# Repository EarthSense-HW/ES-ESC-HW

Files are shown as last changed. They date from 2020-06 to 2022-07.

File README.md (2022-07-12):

# ES-ESC-HW
Hardware source files for EarthSense ESC Based on VESC4

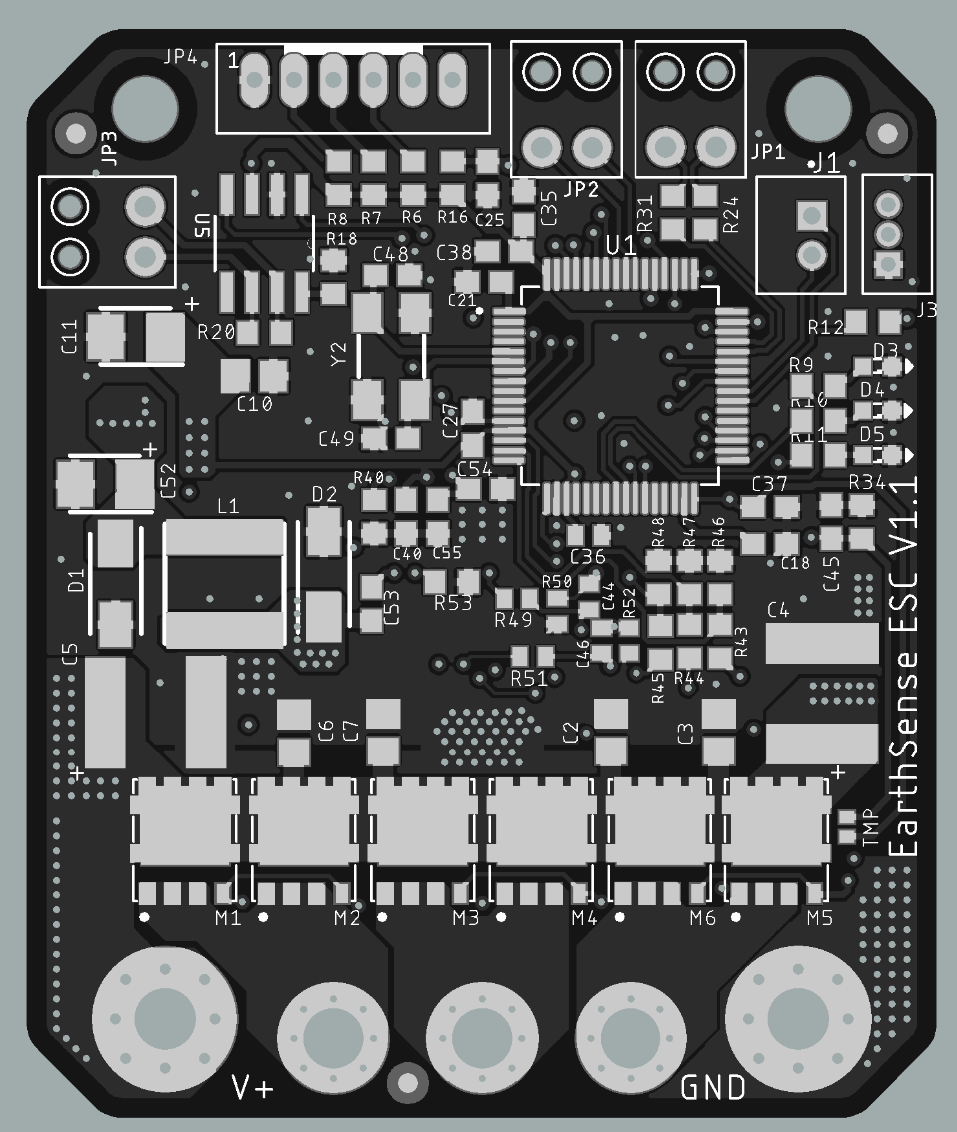
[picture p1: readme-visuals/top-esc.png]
top view

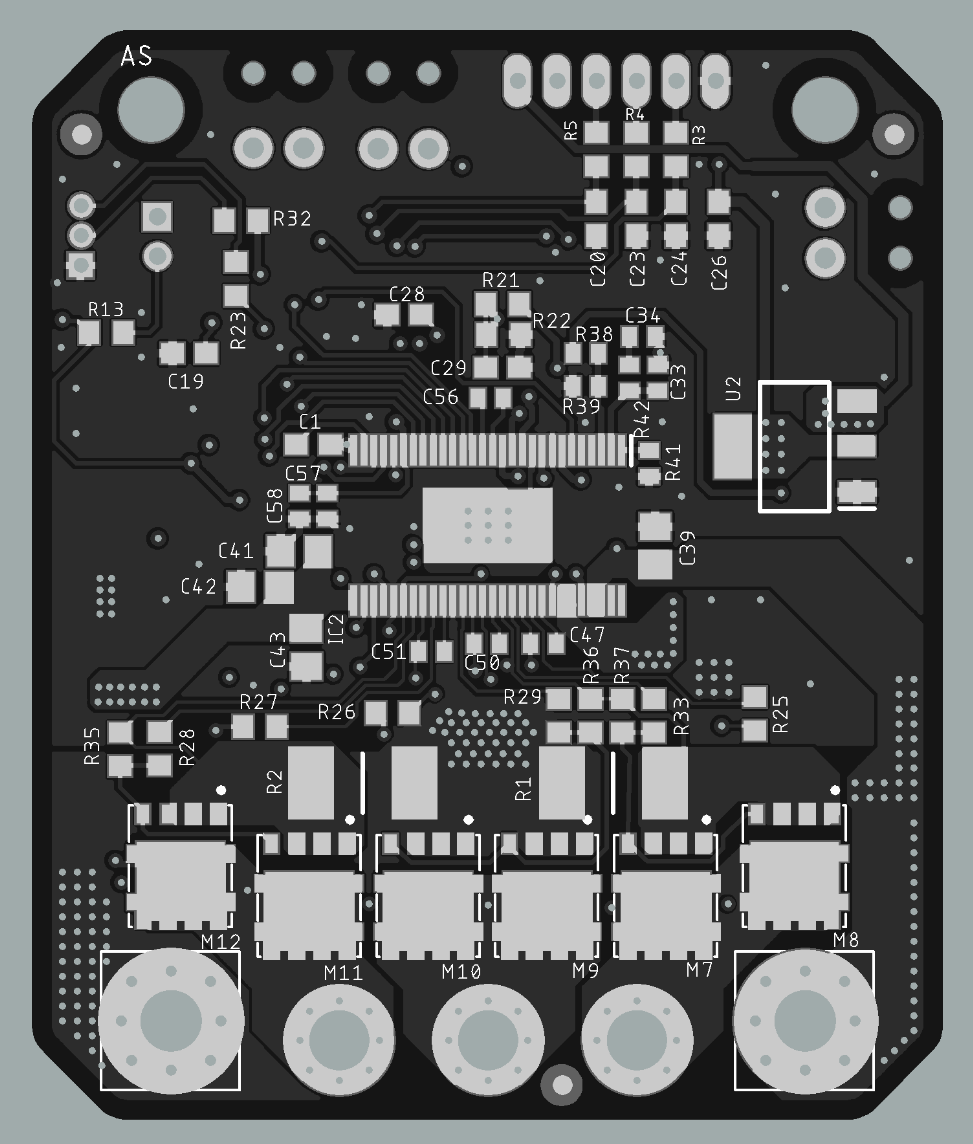
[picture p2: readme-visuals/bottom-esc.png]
bottom view


## Modifications from VESC4 Hardware:
* Changed form factor to fit onto EarthSense TerraSentia System Board
* Two IO Pins are broken out for auto-setting CAN ID based on placement on EarthSense TerraSentia System Board
* MOSFETs changed to flat 5x6 packages (STL260N)
* Changed various components in 5v regulator and 3.3v regulator circuits
* Removed IO pins that are not useful to EarthSense TerraSentia Robots
* SWD Programming header broken out to JST-ZH connector
* Two DIO broken out to JST-PH Connector for reading quadrature encoders

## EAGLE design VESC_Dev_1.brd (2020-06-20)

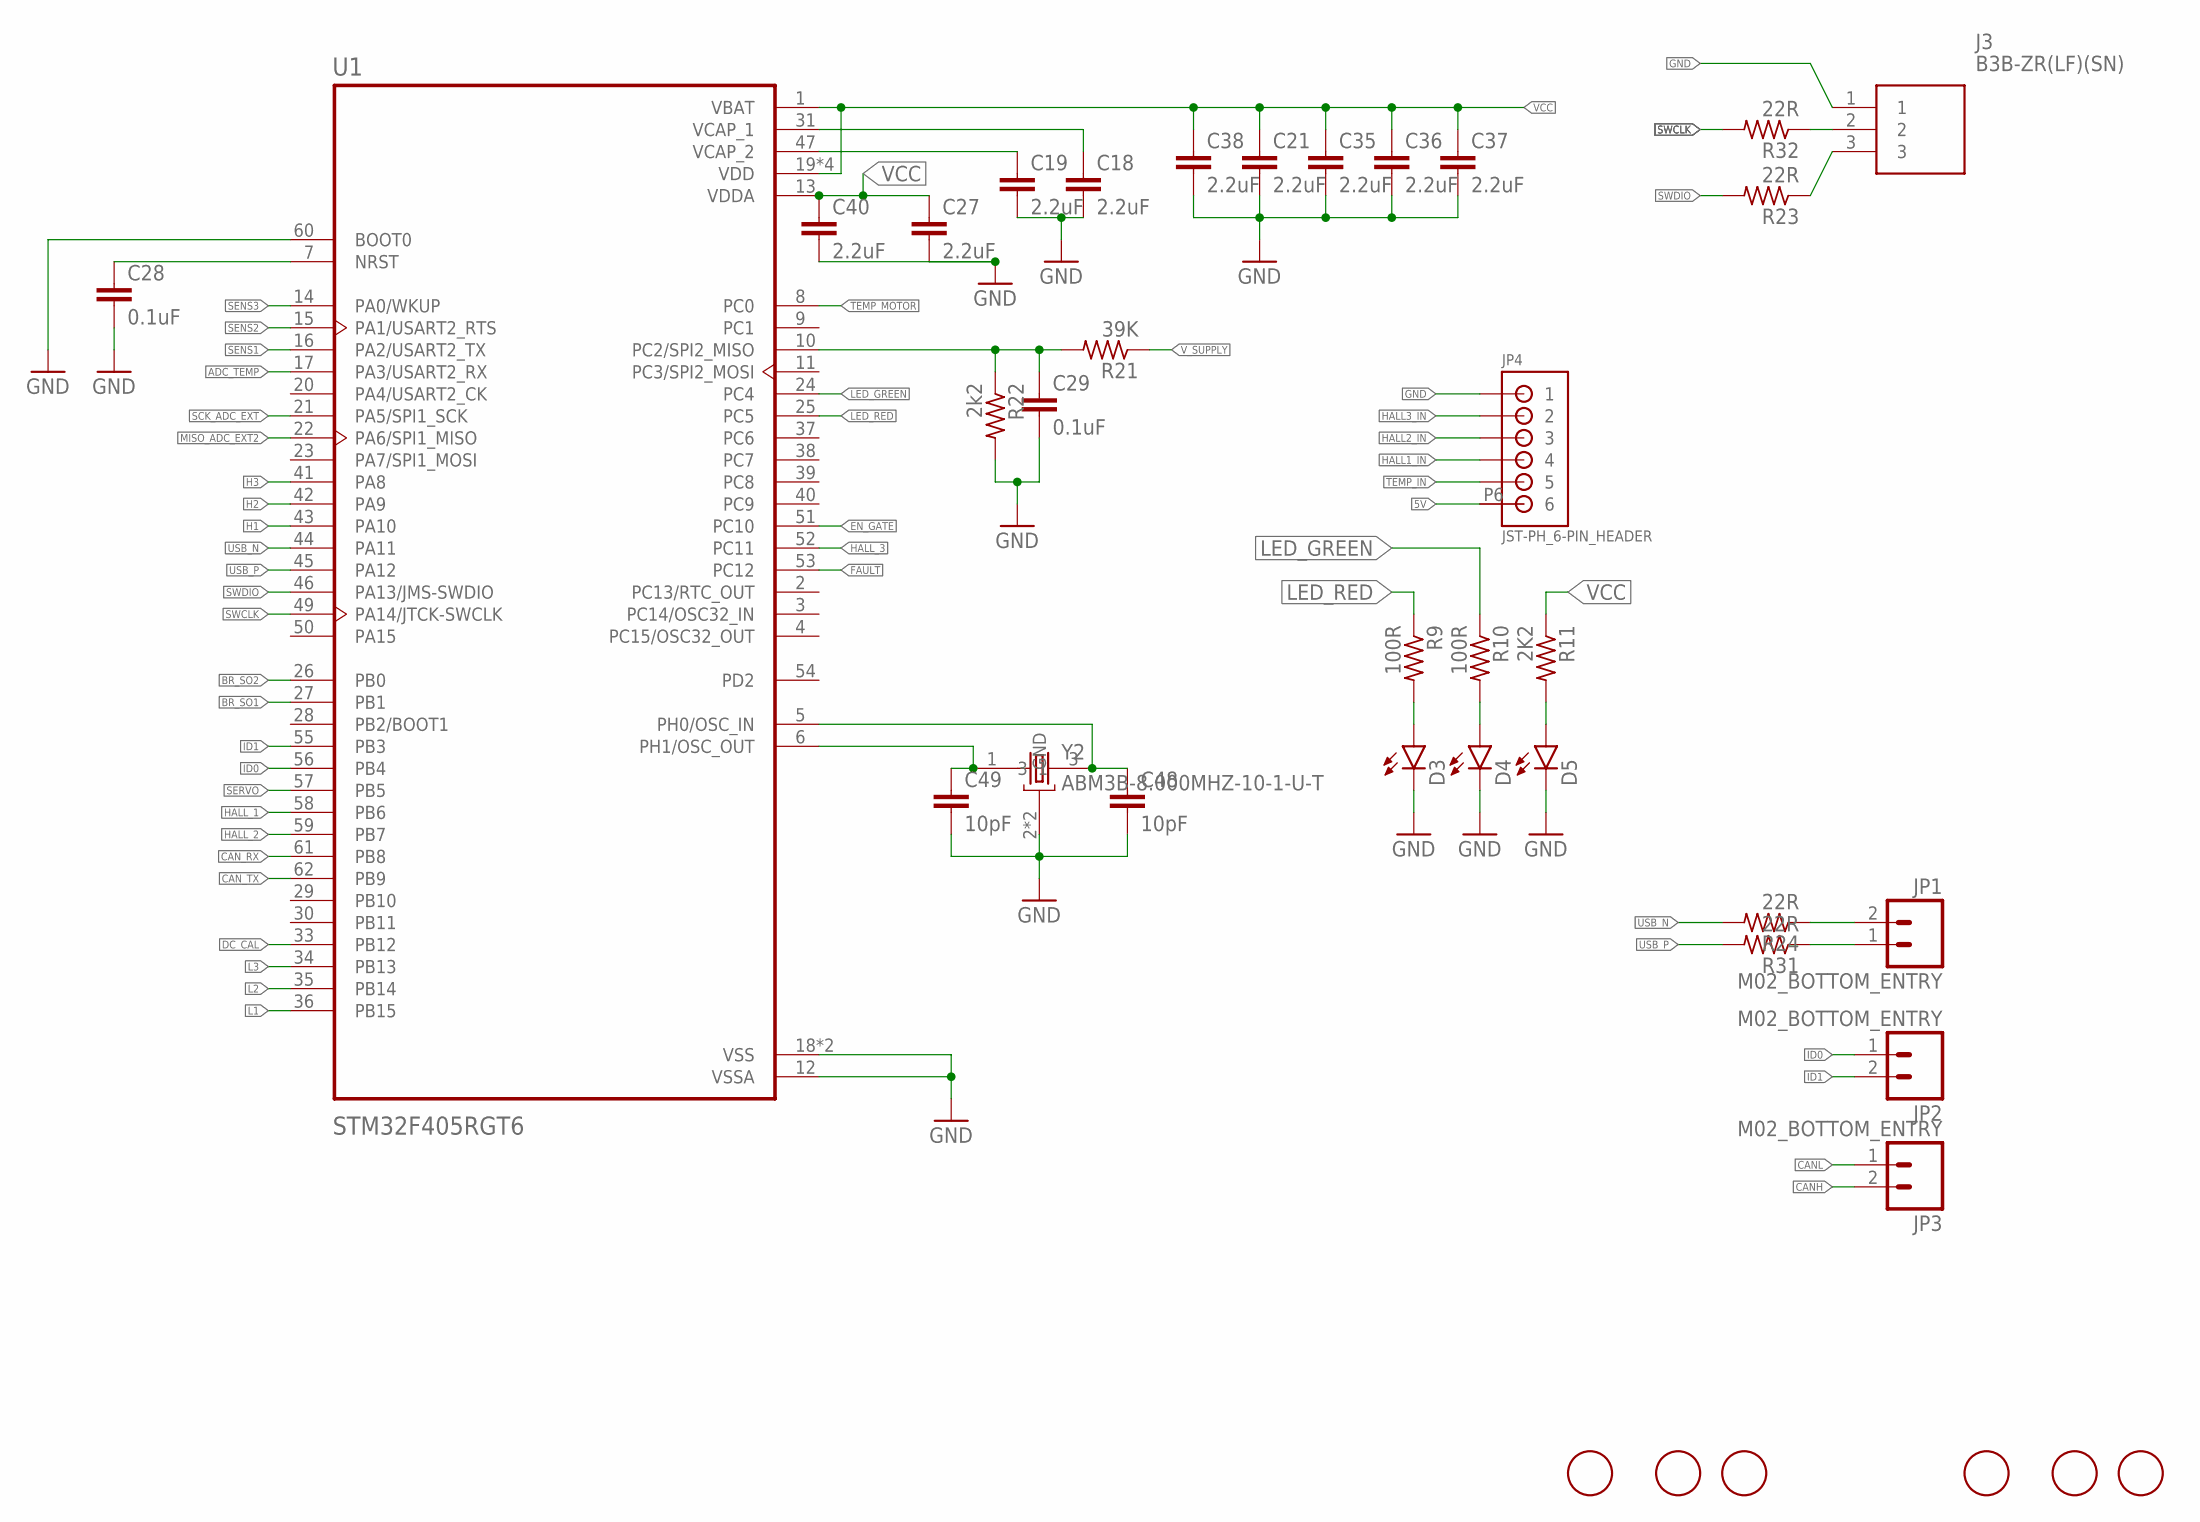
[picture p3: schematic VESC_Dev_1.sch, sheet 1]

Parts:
C18, C19, C21, C27, C35, C37, C38, C40: 2.2uF; C0603
C28, C29: 0.1uF; C0603
C36: 2.2uF; C0402
C48, C49: 10pF; C0603
D3, D4, D5: LEDSML0603; SML0603
J3: B3B-ZR(LF)(SN); SHDR3W50P0X150_1X3_600X350X450
JP1, JP2, JP3: M02_BOTTOM_ENTRY; 1X02_BOTTOM_ENTRY
JP4: JST-PH_6-PIN_HEADER; JST_B6B-PH_HEADER
R9, R10: 100R; R0603
R11: 2K2; R0603
R21: 39K; R0603
R22: 2k2; R0603
R23, R24, R31, R32: 22R; R0603
U1: STM32F405RGT6; QFP50P1200X1200X160-64N
U$1, U$2, U$3, U$4, U$5, U$6: FIDUCIAL; FIDUCIAL_1MM
Y2: ABM3B-8.000MHZ-10-1-U-T; OSCCC500X320X110-4N

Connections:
5V: JP4.P6 (6); also elsewhere on the board
ADC_TEMP: U1.17 (PA3/USART2_RX); also elsewhere on the board
BR_SO1: U1.27 (PB1); also elsewhere on the board
BR_SO2: U1.26 (PB0); also elsewhere on the board
CANH: JP3.2; also elsewhere on the board
CANL: JP3.1; also elsewhere on the board
CAN_RX: U1.61 (PB8); also elsewhere on the board
CAN_TX: U1.62 (PB9); also elsewhere on the board
DC_CAL: U1.33 (PB12); also elsewhere on the board
EN_GATE: U1.51 (PC10); also elsewhere on the board
FAULT: U1.53 (PC12); also elsewhere on the board
GND: C18.2, C19.2, C21.2, C27.2, C28.2, C29.2, C35.2, C36.2, C37.2, C38.2, C40.2, C48.2, C49.2, D3.C, D4.C, D5.C, J3.1, JP4.P1 (1), R22.2, U1.12 (VSSA), U1.18 (VSS), U1.60 (BOOT0), U1.63 (VSS), Y2.2 (GND), Y2.4 (GND); also elsewhere on the board
H1: U1.43 (PA10); also elsewhere on the board
H2: U1.42 (PA9); also elsewhere on the board
H3: U1.41 (PA8); also elsewhere on the board
HALL1_IN: JP4.P4 (4); also elsewhere on the board
HALL2_IN: JP4.P3 (3); also elsewhere on the board
HALL3_IN: JP4.P2 (2); also elsewhere on the board
HALL_1: U1.58 (PB6); also elsewhere on the board
HALL_2: U1.59 (PB7); also elsewhere on the board
HALL_3: U1.52 (PC11); also elsewhere on the board
ID0: JP2.1, U1.56 (PB4)
ID1: JP2.2, U1.55 (PB3)
L1: U1.36 (PB15); also elsewhere on the board
L2: U1.35 (PB14); also elsewhere on the board
L3: U1.34 (PB13); also elsewhere on the board
LED_GREEN: R10.1, U1.24 (PC4)
LED_RED: R9.1, U1.25 (PC5)
MISO_ADC_EXT2: U1.22 (PA6/SPI1_MISO)
unnamed: C28.1, U1.7 (NRST)
unnamed: J3.2, R32.1
unnamed: C29.1, R21.2, R22.1, U1.10 (PC2/SPI2_MISO)
unnamed: JP1.2, R24.1
unnamed: C18.1, U1.31 (VCAP_1)
unnamed: JP1.1, R31.1
unnamed: C19.1, U1.47 (VCAP_2)
unnamed: C49.1, U1.6 (PH1/OSC_OUT), Y2.1
unnamed: C48.1, U1.5 (PH0/OSC_IN), Y2.3
unnamed: J3.3, R23.1
unnamed: D3.A, R9.2
unnamed: D4.A, R10.2
unnamed: D5.A, R11.2
SCK_ADC_EXT: U1.21 (PA5/SPI1_SCK)
SENS1: U1.16 (PA2/USART2_TX); also elsewhere on the board
SENS2: U1.15 (PA1/USART2_RTS); also elsewhere on the board
SENS3: U1.14 (PA0/WKUP); also elsewhere on the board
SERVO: U1.57 (PB5)
SWCLK: R32.2, U1.49 (PA14/JTCK-SWCLK)
SWDIO: R23.2, U1.46 (PA13/JMS-SWDIO)
TEMP_IN: JP4.P5 (5)
TEMP_MOTOR: U1.8 (PC0); also elsewhere on the board
USB_N: R24.2, U1.44 (PA11)
USB_P: R31.2, U1.45 (PA12)
VCC: C21.1, C27.1, C35.1, C36.1, C37.1, C38.1, C40.1, R11.1, U1.1 (VBAT), U1.13 (VDDA), U1.19 (VDD), U1.32 (VDD), U1.48 (VDD), U1.64 (VDD); also elsewhere on the board
V_SUPPLY: R21.1; also elsewhere on the board

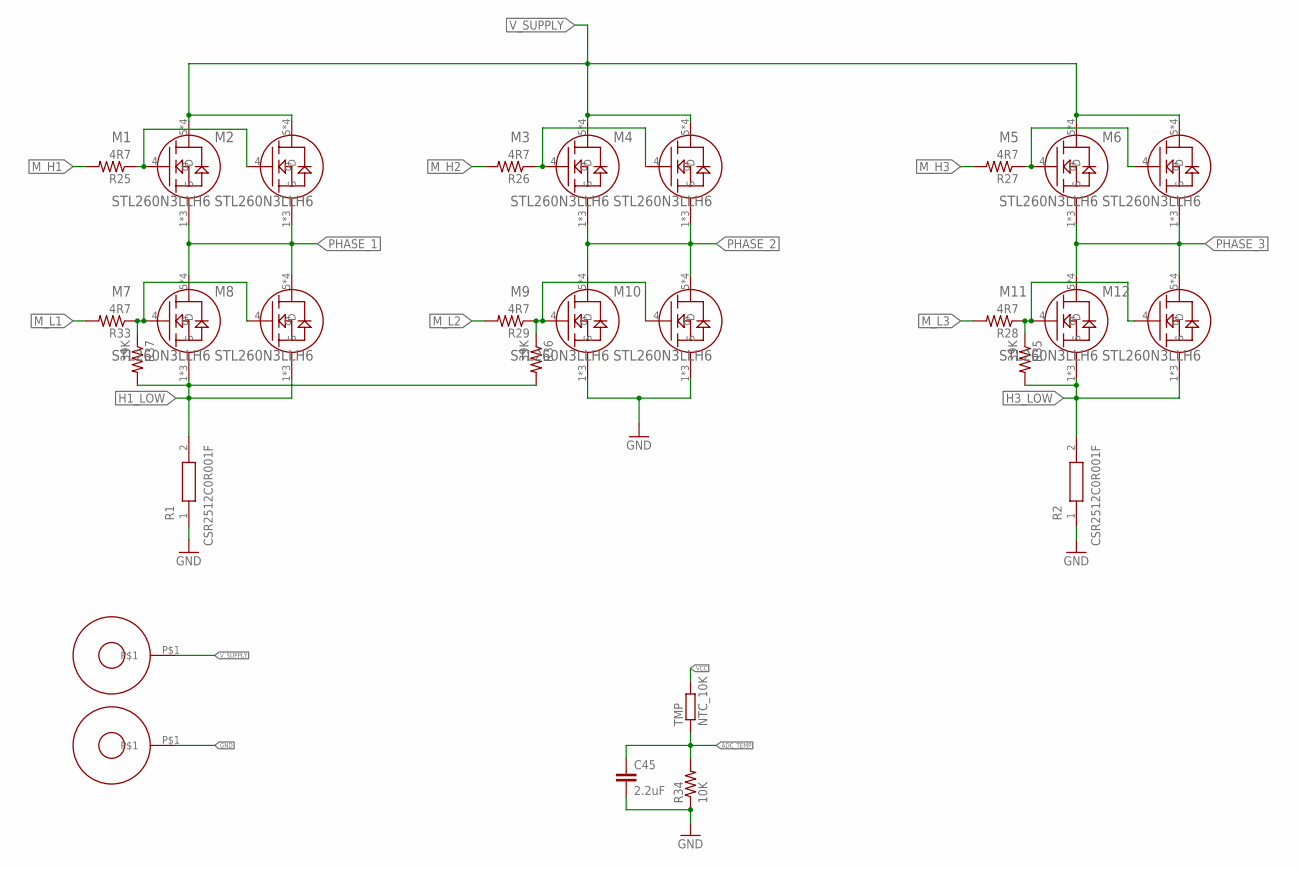
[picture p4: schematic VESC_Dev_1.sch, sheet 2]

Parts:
C45: 2.2uF; C0603
M1, M2, M3, M4, M5, M6, M7, M8, M9, M10, M11, M12: STL260N3LLH6; TRANS_STL60P4LLF6
R1, R2: CSR2512C0R001F; RESC6432X85N
R25, R26, R27, R28, R29, R33: 4R7; R0603
R34: 10K; R0603
R35, R36, R37: 39K; R0603
TMP: NTC_10K; R0402
U$7, U$8: M3_POWER_HOLE

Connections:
ADC_TEMP: C45.1, R34.2, TMP.1; also elsewhere on the board
GND: C45.2, M9.1 (S), M9.2 (S), M9.3 (S), M10.1 (S), M10.2 (S), M10.3 (S), R1.1, R2.1, R34.1, U$8.P$1; also elsewhere on the board
H1_LOW: M7.1 (S), M7.2 (S), M7.3 (S), M8.1 (S), M8.2 (S), M8.3 (S), R1.2, R36.2, R37.2; also elsewhere on the board
H3_LOW: M11.1 (S), M11.2 (S), M11.3 (S), M12.1 (S), M12.2 (S), M12.3 (S), R2.2, R35.2; also elsewhere on the board
M_H1: R25.2; also elsewhere on the board
M_H2: R26.2; also elsewhere on the board
M_H3: R27.2; also elsewhere on the board
M_L1: R33.2; also elsewhere on the board
M_L2: R29.2; also elsewhere on the board
M_L3: R28.2; also elsewhere on the board
unnamed: M1.4 (G), M2.4 (G), R25.1
unnamed: M11.4 (G), M12.4 (G), R28.1, R35.1
unnamed: M7.4 (G), M8.4 (G), R33.1, R37.1
unnamed: M3.4 (G), M4.4 (G), R26.1
unnamed: M9.4 (G), M10.4 (G), R29.1, R36.1
unnamed: M5.4 (G), M6.4 (G), R27.1
PHASE_1: M1.1 (S), M1.2 (S), M1.3 (S), M2.1 (S), M2.2 (S), M2.3 (S), M7.5 (D), M7.6 (D), M7.7 (D), M7.8 (D), M8.5 (D), M8.6 (D), M8.7 (D), M8.8 (D); also elsewhere on the board
PHASE_2: M3.1 (S), M3.2 (S), M3.3 (S), M4.1 (S), M4.2 (S), M4.3 (S), M9.5 (D), M9.6 (D), M9.7 (D), M9.8 (D), M10.5 (D), M10.6 (D), M10.7 (D), M10.8 (D); also elsewhere on the board
PHASE_3: M5.1 (S), M5.2 (S), M5.3 (S), M6.1 (S), M6.2 (S), M6.3 (S), M11.5 (D), M11.6 (D), M11.7 (D), M11.8 (D), M12.5 (D), M12.6 (D), M12.7 (D), M12.8 (D); also elsewhere on the board
VCC: TMP.2; also elsewhere on the board
V_SUPPLY: M1.5 (D), M1.6 (D), M1.7 (D), M1.8 (D), M2.5 (D), M2.6 (D), M2.7 (D), M2.8 (D), M3.5 (D), M3.6 (D), M3.7 (D), M3.8 (D), M4.5 (D), M4.6 (D), M4.7 (D), M4.8 (D), M5.5 (D), M5.6 (D), M5.7 (D), M5.8 (D), M6.5 (D), M6.6 (D), M6.7 (D), M6.8 (D), U$7.P$1; also elsewhere on the board

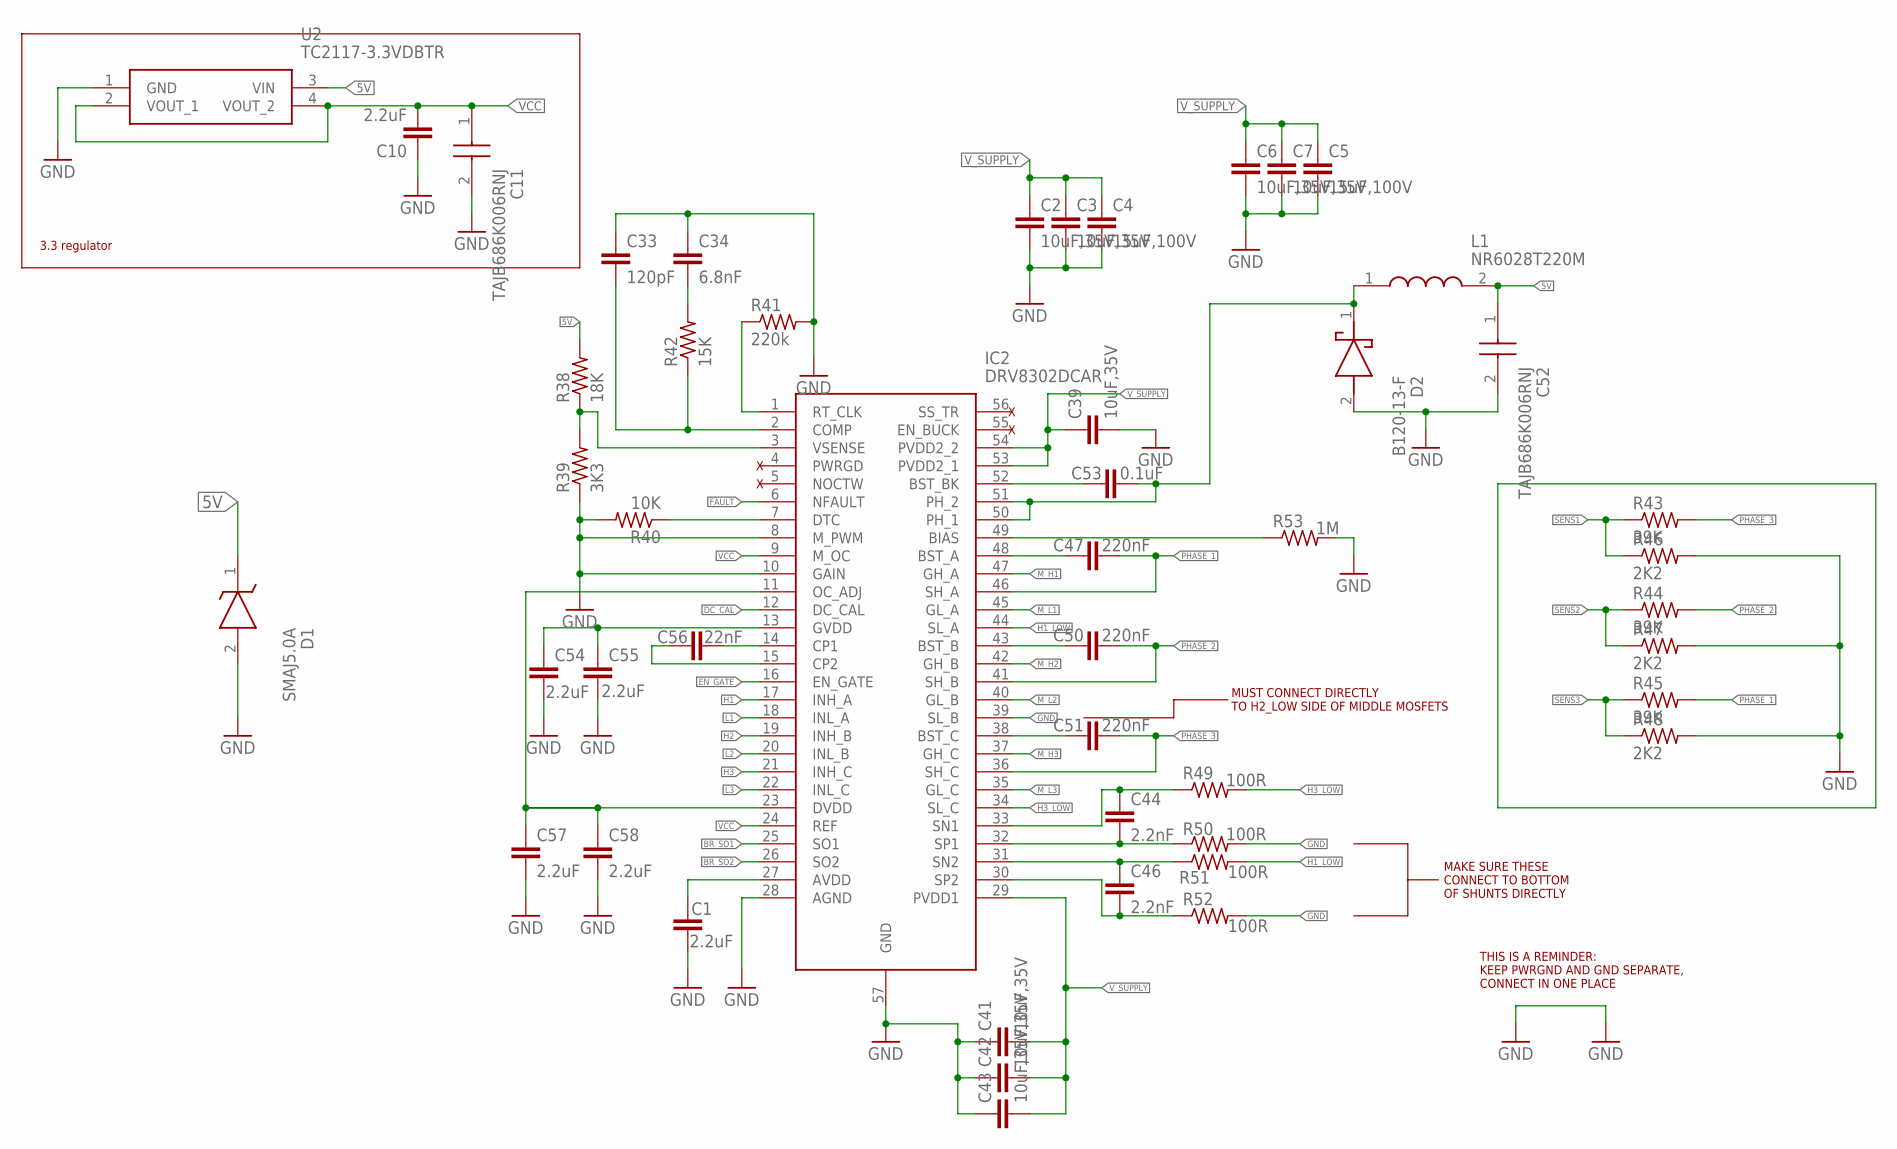
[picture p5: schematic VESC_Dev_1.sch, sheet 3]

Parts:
C1, C54, C55: 2.2uF; C0603
C2, C3, C6, C7, C39, C41, C42, C43: 10uF,35V; C0805
C4, C5: 15uF,100V; C2220K
C10: 2.2uF; C0805
C11, C52: TAJB686K006RNJ; CAPPM3528X210N
C33: 120pF; C0402
C34: 6.8nF; C0402
C44, C46: 2.2nF; C0402
C47, C50, C51: 220nF; C0402
C53: 0.1uF; C0603
C56: 22nF; C0402
C57, C58: 2.2uF; C0402
D1: SMAJ5.0A; DIOM5026X229N
D2: B120-13-F; DIOM5226X240N
IC2: DRV8302DCAR; SOP50P810X120-57N
L1: NR6028T220M
R38: 18K; R0402
R39: 3K3; R0402
R40: 10K; R0603
R41: 220k; R0402
R42: 15K; R0402
R43, R44, R45: 39K; R0603
R46, R47, R48: 2K2; R0603
R49, R50, R51, R52: 100R; R0402
R53: 1M; R0603
U2: TC2117-3.3VDBTR; SOT230P700X180-4N

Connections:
5V: C52.1 (+), D1.1 (K), L1.2, R38.2, U2.3 (VIN); also elsewhere on the board
BR_SO1: IC2.25 (SO1); also elsewhere on the board
BR_SO2: IC2.26 (SO2); also elsewhere on the board
DC_CAL: IC2.12 (DC_CAL); also elsewhere on the board
EN_GATE: IC2.16 (EN_GATE); also elsewhere on the board
FAULT: IC2.6 (NFAULT); also elsewhere on the board
GND: C1.2, C2.2, C3.2, C4.2, C5.2, C6.2, C7.2, C10.1, C11.2 (-), C33.1, C34.1, C39.2, C41.1, C42.1, C43.1, C52.2 (-), C54.2, C55.2, C57.2, C58.2, D1.2 (A), D2.2 (A), IC2.8 (M_PWM), IC2.10 (GAIN), IC2.28 (AGND), IC2.39 (SL_B), IC2.57 (GND), R39.1, R40.2, R41.2, R46.2, R47.2, R48.2, R50.2, R52.2, R53.2, U2.1 (GND); also elsewhere on the board
H1: IC2.17 (INH_A); also elsewhere on the board
H1_LOW: IC2.44 (SL_A), R51.2; also elsewhere on the board
H2: IC2.19 (INH_B); also elsewhere on the board
H3: IC2.21 (INH_C); also elsewhere on the board
H3_LOW: IC2.34 (SL_C), R49.2; also elsewhere on the board
L1: IC2.18 (INL_A); also elsewhere on the board
L2: IC2.20 (INL_B); also elsewhere on the board
L3: IC2.22 (INL_C); also elsewhere on the board
M_H1: IC2.47 (GH_A); also elsewhere on the board
M_H2: IC2.42 (GH_B); also elsewhere on the board
M_H3: IC2.37 (GH_C); also elsewhere on the board
M_L1: IC2.45 (GL_A); also elsewhere on the board
M_L2: IC2.40 (GL_B); also elsewhere on the board
M_L3: IC2.35 (GL_C); also elsewhere on the board
unnamed: C57.1, C58.1, IC2.11 (OC_ADJ), IC2.23 (DVDD)
unnamed: IC2.3 (VSENSE), R38.1, R39.2
unnamed: IC2.7 (DTC), R40.1
unnamed: C54.1, C55.1, IC2.13 (GVDD)
unnamed: C56.2, IC2.14 (CP1)
unnamed: C56.1, IC2.15 (CP2)
unnamed: IC2.1 (RT_CLK), R41.1
unnamed: C33.2, IC2.2 (COMP), R42.1
unnamed: C34.2, R42.2
unnamed: C1.1, IC2.27 (AVDD)
unnamed: IC2.49 (BIAS), R53.1
unnamed: C46.2, IC2.30 (SP2), R52.1
unnamed: C46.1, IC2.31 (SN2), R51.1
unnamed: C44.1, IC2.33 (SN1), R49.1
unnamed: C44.2, IC2.32 (SP1), R50.1
unnamed: C51.1, IC2.38 (BST_C)
unnamed: C50.1, IC2.43 (BST_B)
unnamed: C47.1, IC2.48 (BST_A)
unnamed: C53.1, IC2.52 (BST_BK)
unnamed: C53.2, D2.1 (K), IC2.50 (PH_1), IC2.51 (PH_2), L1.1
PHASE_1: C47.2, IC2.46 (SH_A), R45.2; also elsewhere on the board
PHASE_2: C50.2, IC2.41 (SH_B), R44.2; also elsewhere on the board
PHASE_3: C51.2, IC2.36 (SH_C), R43.2; also elsewhere on the board
SENS1: R43.1, R46.1; also elsewhere on the board
SENS2: R44.1, R47.1; also elsewhere on the board
SENS3: R45.1, R48.1; also elsewhere on the board
VCC: C10.2, C11.1 (+), IC2.9 (M_OC), IC2.24 (REF), U2.2 (VOUT_1), U2.4 (VOUT_2); also elsewhere on the board
V_SUPPLY: C2.1, C3.1, C4.1, C5.1, C6.1, C7.1, C39.1, C41.2, C42.2, C43.2, IC2.29 (PVDD1), IC2.53 (PVDD2_1), IC2.54 (PVDD2_2); also elsewhere on the board

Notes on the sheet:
3.3 regulator
MAKE SURE THESE CONNECT TO BOTTOM OF SHUNTS DIRECTLY
THIS IS A REMINDER: KEEP PWRGND AND GND SEPARATE, CONNECT IN ONE PLACE
MUST CONNECT DIRECTLY TO H2_LOW SIDE OF MIDDLE MOSFETS

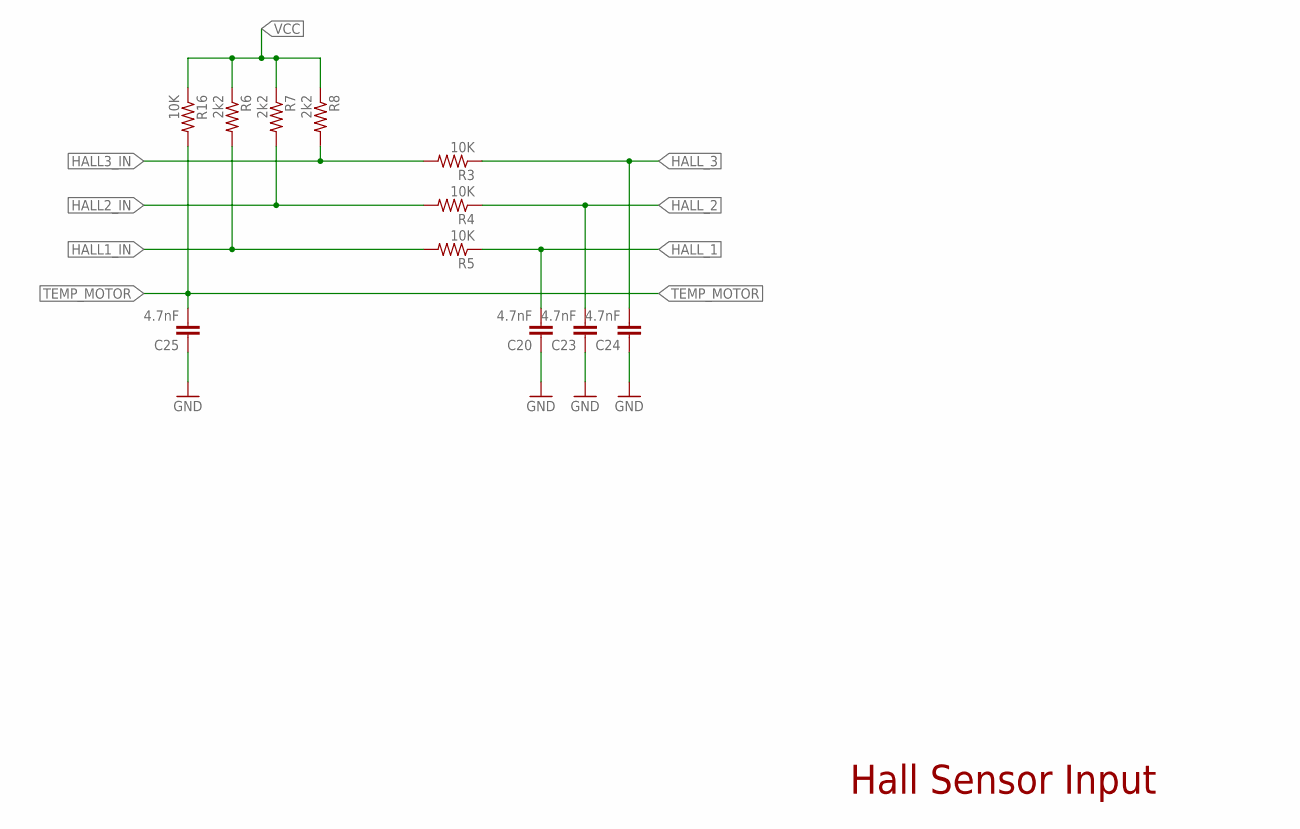
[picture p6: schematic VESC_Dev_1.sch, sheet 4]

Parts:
C20, C23, C24, C25: 4.7nF; C0603
R3, R4, R5, R16: 10K; R0603
R6, R7, R8: 2k2; R0603

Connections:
GND: C20.1, C23.1, C24.1, C25.1; also elsewhere on the board
HALL1_IN: R5.2, R6.2; also elsewhere on the board
HALL2_IN: R4.2, R7.2; also elsewhere on the board
HALL3_IN: R3.2, R8.2; also elsewhere on the board
HALL_1: C20.2, R5.1; also elsewhere on the board
HALL_2: C23.2, R4.1; also elsewhere on the board
HALL_3: C24.2, R3.1; also elsewhere on the board
TEMP_MOTOR: C25.2, R16.2; also elsewhere on the board
VCC: R6.1, R7.1, R8.1, R16.1; also elsewhere on the board

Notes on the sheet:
Hall Sensor Input

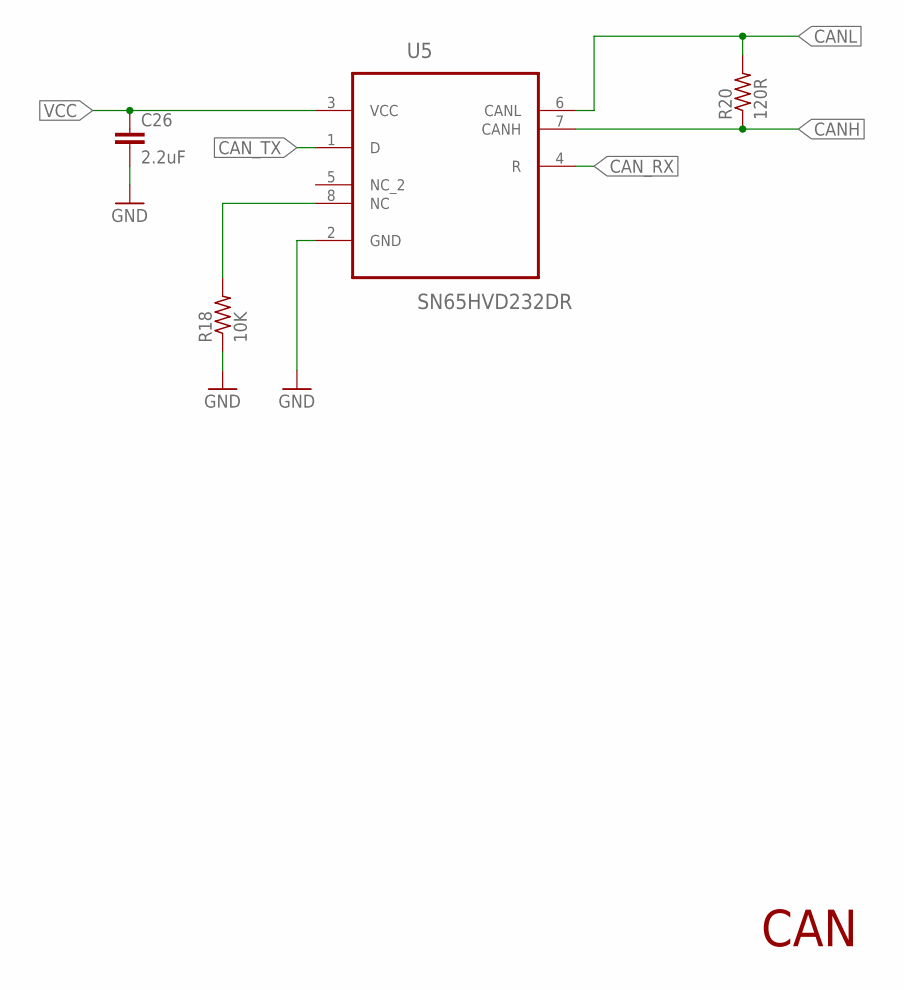
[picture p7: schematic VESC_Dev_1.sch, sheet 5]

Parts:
C26: 2.2uF; C0603
R18: 10K; R0603
R20: 120R; R0603
U5: SN65HVD232DR; SOIC127P600X175-8N

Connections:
CANH: R20.1, U5.7 (CANH); also elsewhere on the board
CANL: R20.2, U5.6 (CANL); also elsewhere on the board
CAN_RX: U5.4 (R); also elsewhere on the board
CAN_TX: U5.1 (D); also elsewhere on the board
GND: C26.2, R18.1, U5.2 (GND); also elsewhere on the board
unnamed: R18.2, U5.8 (NC)
VCC: C26.1, U5.3 (VCC); also elsewhere on the board

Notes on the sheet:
CAN

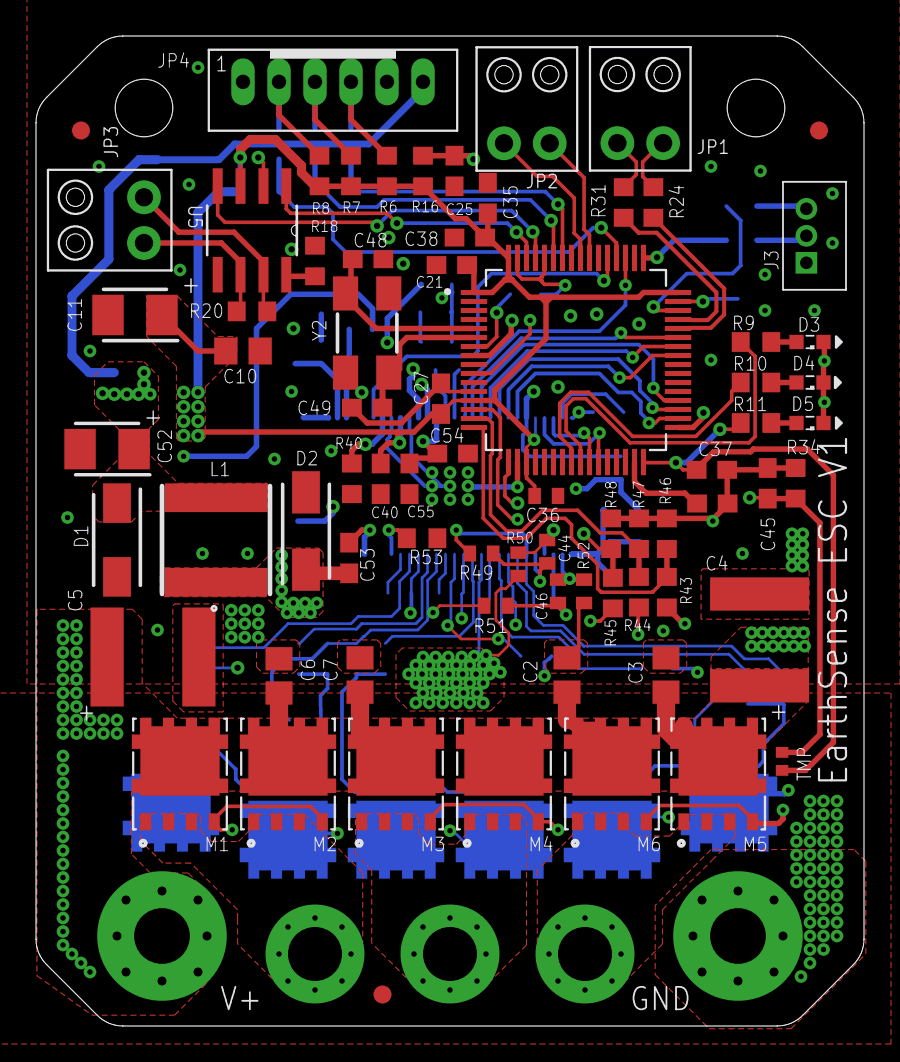
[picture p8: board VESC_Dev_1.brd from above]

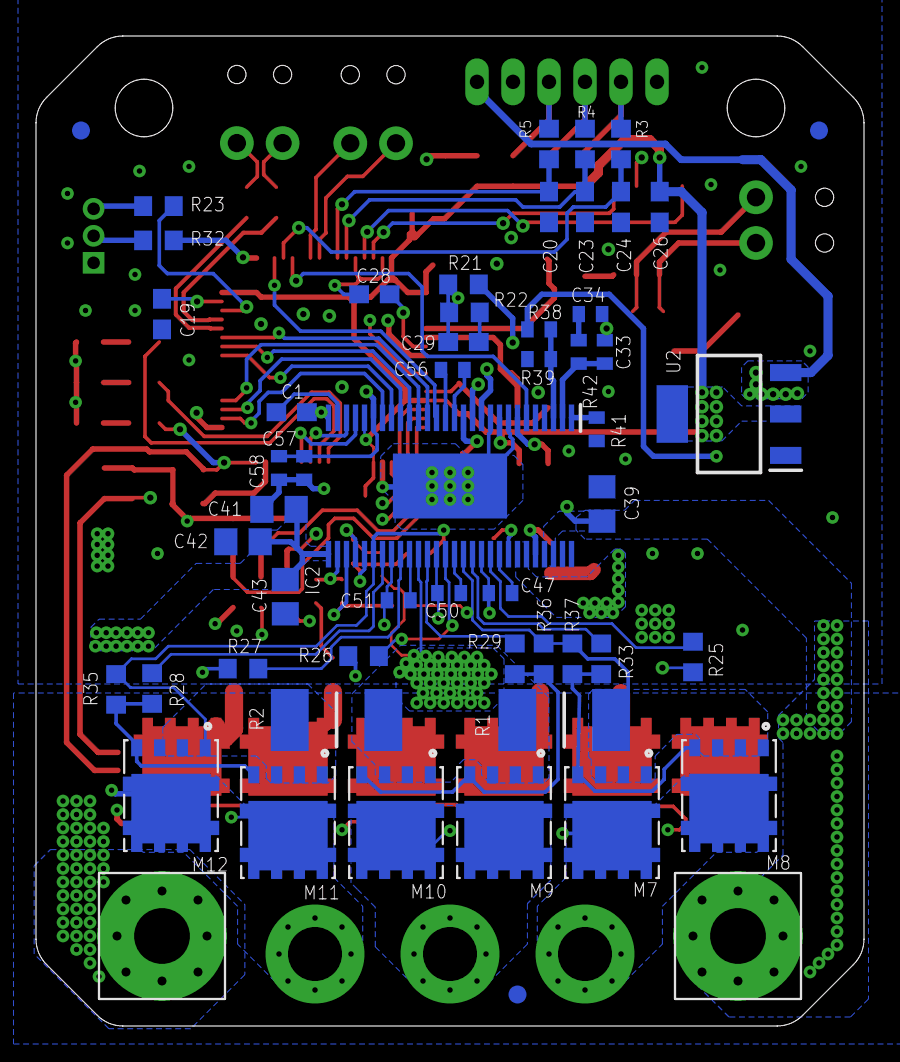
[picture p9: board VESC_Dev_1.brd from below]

Board: 4 copper layers, 46.0 x 55.0 mm, 129 parts (53 on the bottom side), 89 nets.

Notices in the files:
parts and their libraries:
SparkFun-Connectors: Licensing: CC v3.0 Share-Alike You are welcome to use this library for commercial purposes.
